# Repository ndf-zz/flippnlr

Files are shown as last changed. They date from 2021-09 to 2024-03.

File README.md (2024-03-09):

# Flippnlr - 4x5 DiY Flipdot Panel

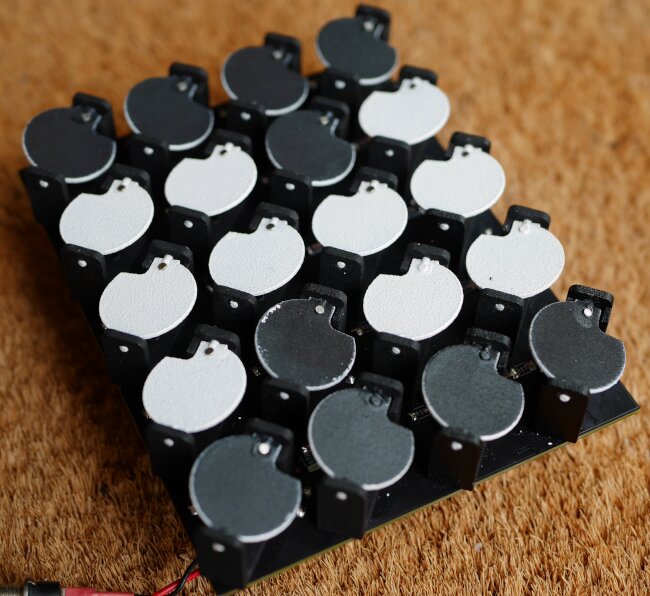
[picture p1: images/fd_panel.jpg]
Panel 4x5 Panel 4x5`


How _not_ to make a DiY electromechanical "Flip-Dot" matrix display.

## Coil Winding

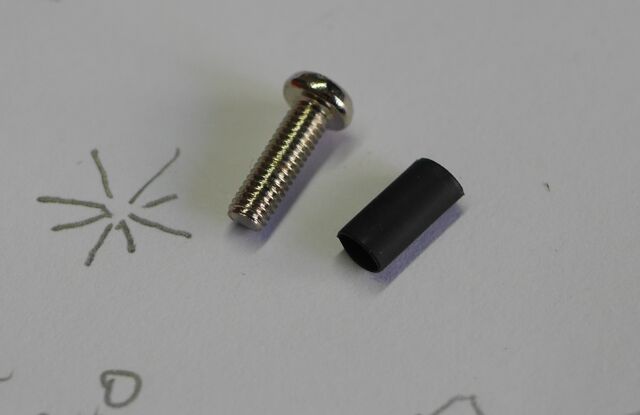
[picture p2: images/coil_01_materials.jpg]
Screw


M3 steel screw and heat shrink tube.

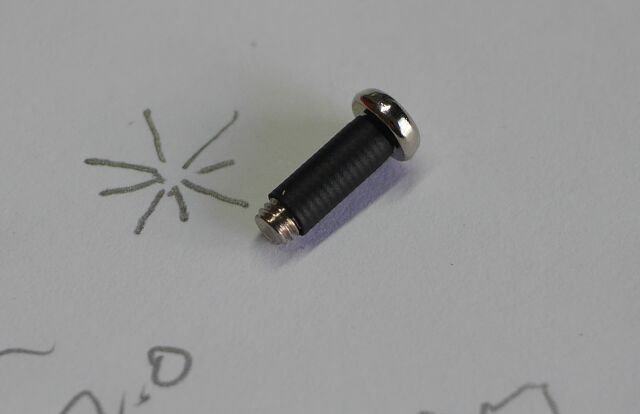
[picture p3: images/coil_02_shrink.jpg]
Shrink


Shrink onto screw.

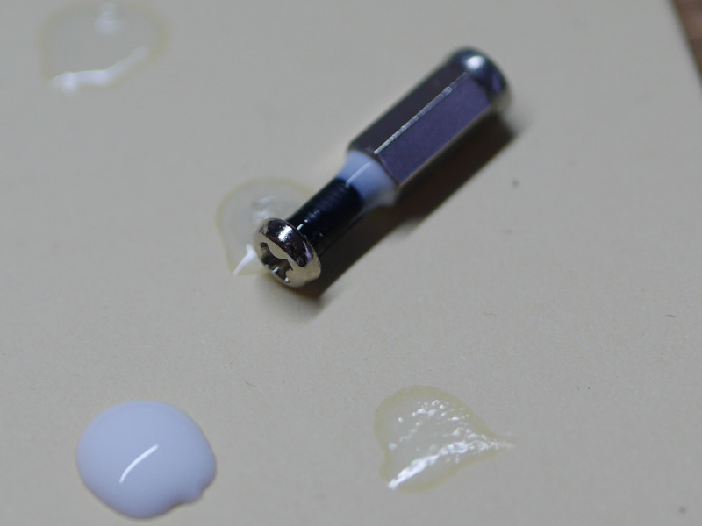
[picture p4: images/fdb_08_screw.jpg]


Add slight glue fillet.

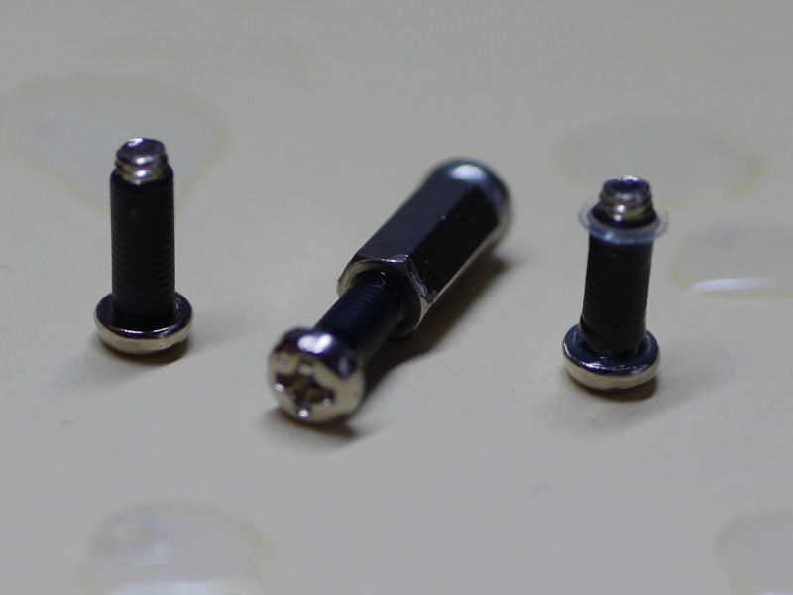
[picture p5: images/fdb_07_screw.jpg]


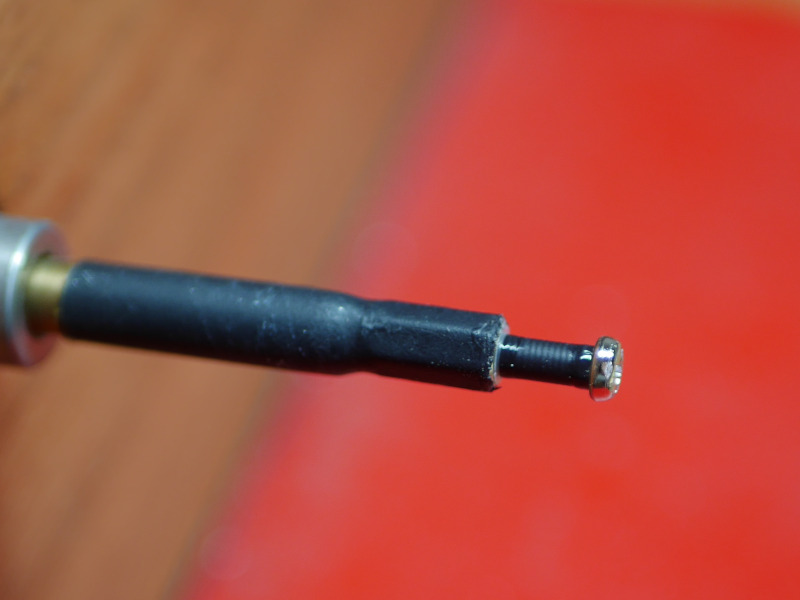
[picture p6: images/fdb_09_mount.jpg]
Mount


Mount in winder.

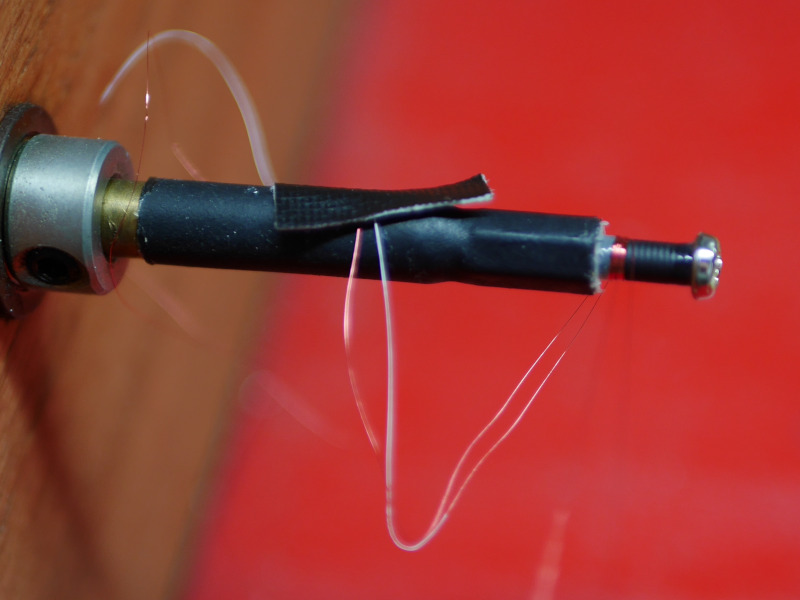
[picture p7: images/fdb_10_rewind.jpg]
Start Wires


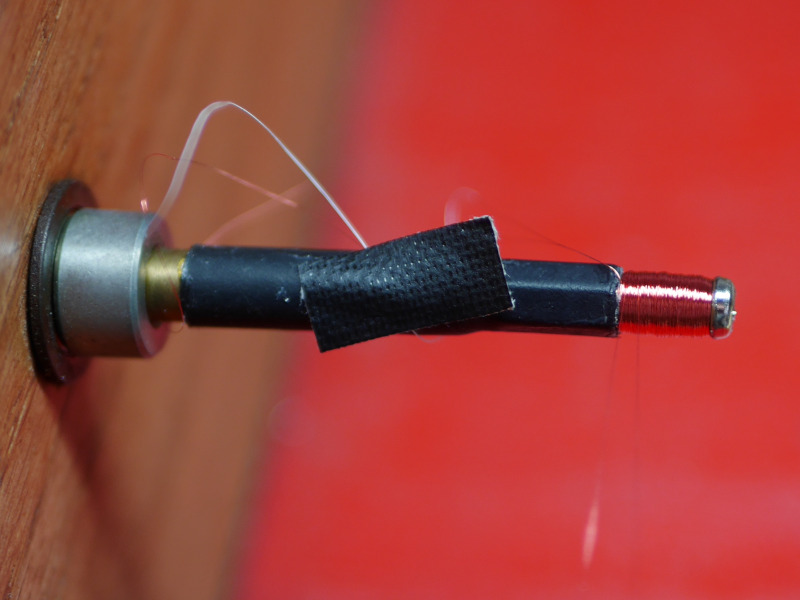
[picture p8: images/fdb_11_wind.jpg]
1000 Turns


Wind about 1000 turns.

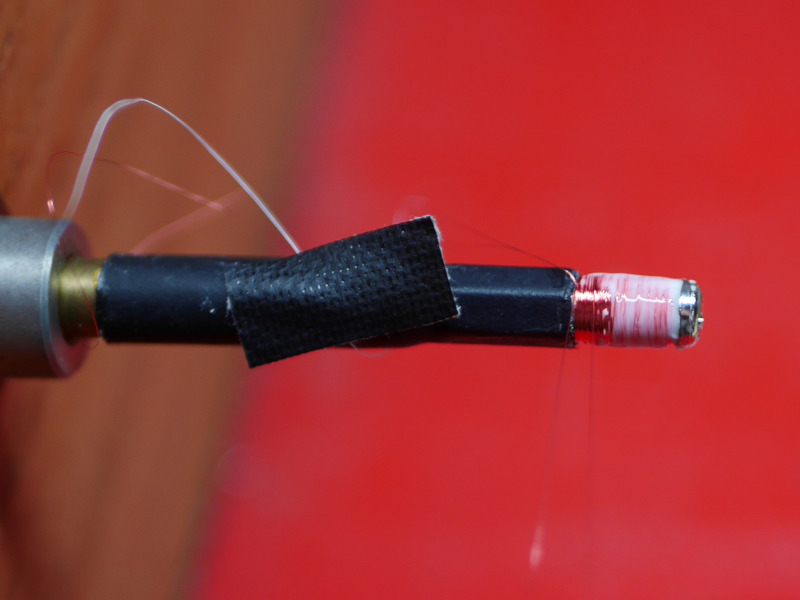
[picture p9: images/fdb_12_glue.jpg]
Glue Coil


Finish with a thin layer of glue.

## Flipdot Mechanism

FreeCAD model: [flipdot.FCStd](flipdot.FCStd)

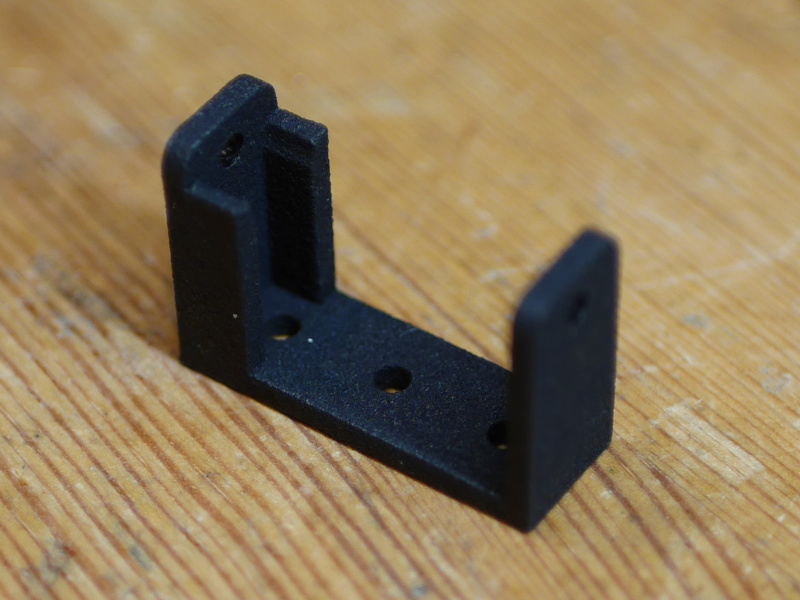
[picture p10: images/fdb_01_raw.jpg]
SLS Body


SLS printed housing.

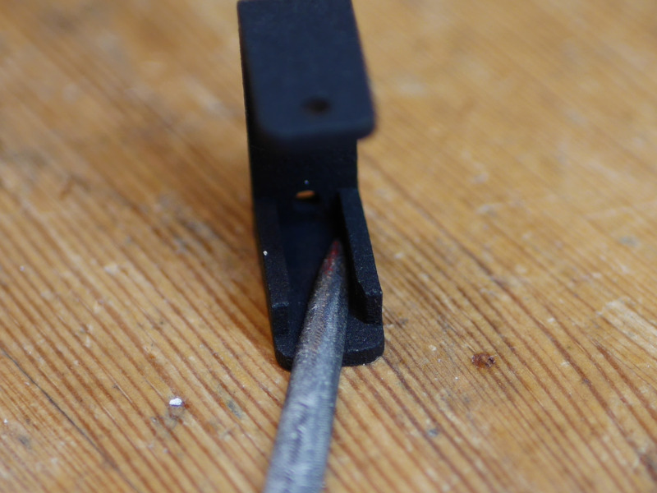
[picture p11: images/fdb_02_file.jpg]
File Housing


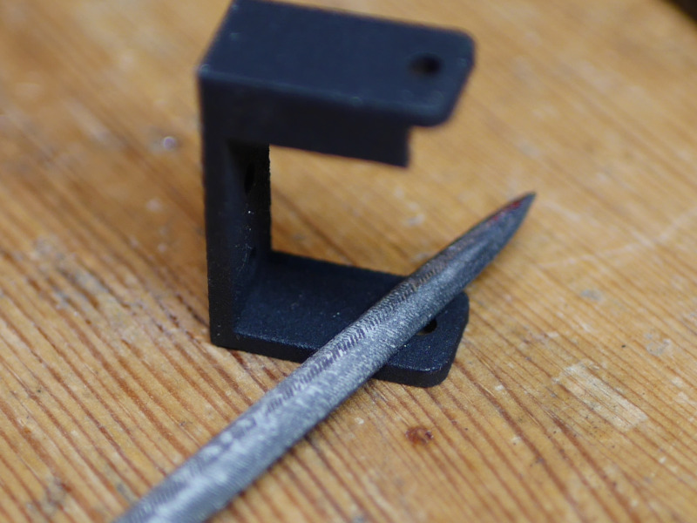
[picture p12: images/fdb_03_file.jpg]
File Mount


File contact areas.

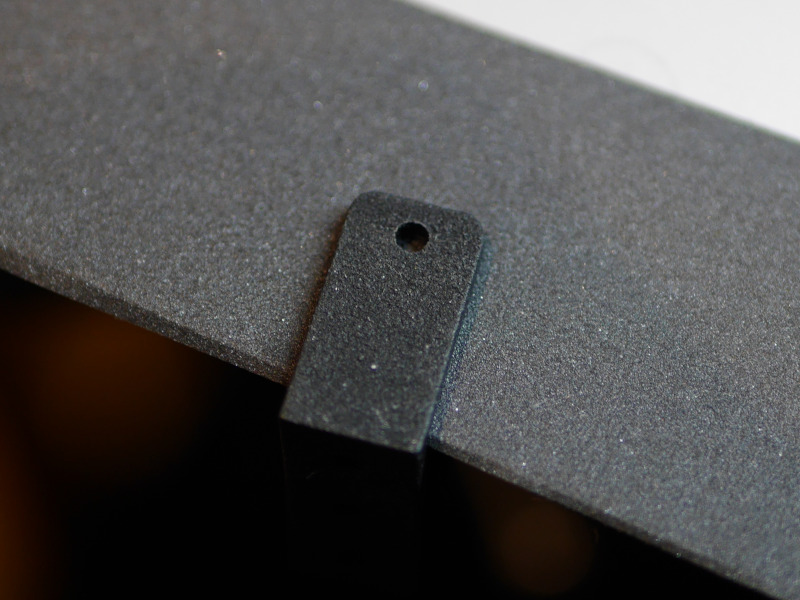
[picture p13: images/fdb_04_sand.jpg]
Smooth Mount


Smooth contact areas with fine sandpaper.

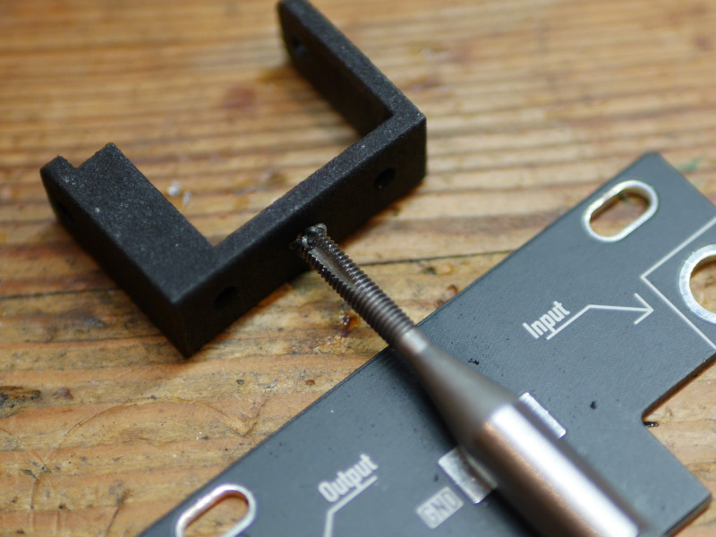
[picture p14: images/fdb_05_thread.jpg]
Tap Mounting Hole


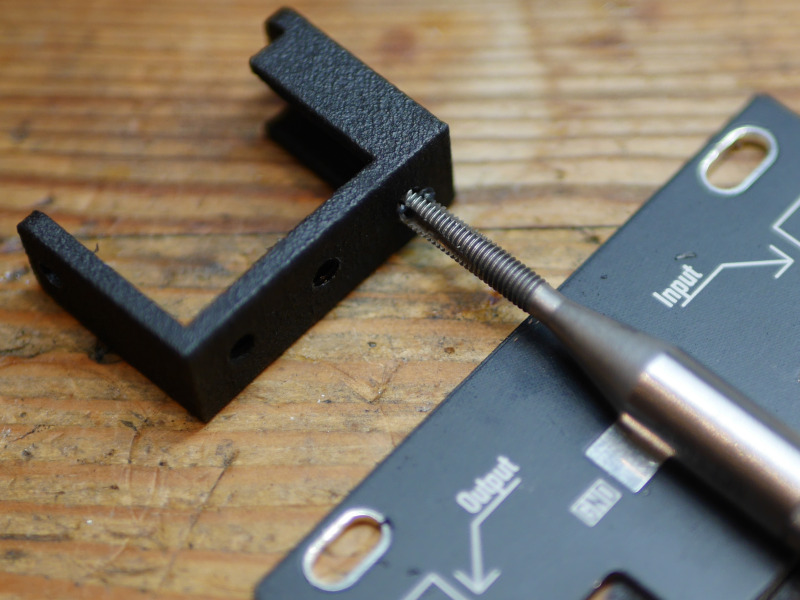
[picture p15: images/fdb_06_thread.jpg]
Tap Coil Hole


Tap mounting and coil holes with M3 thread.

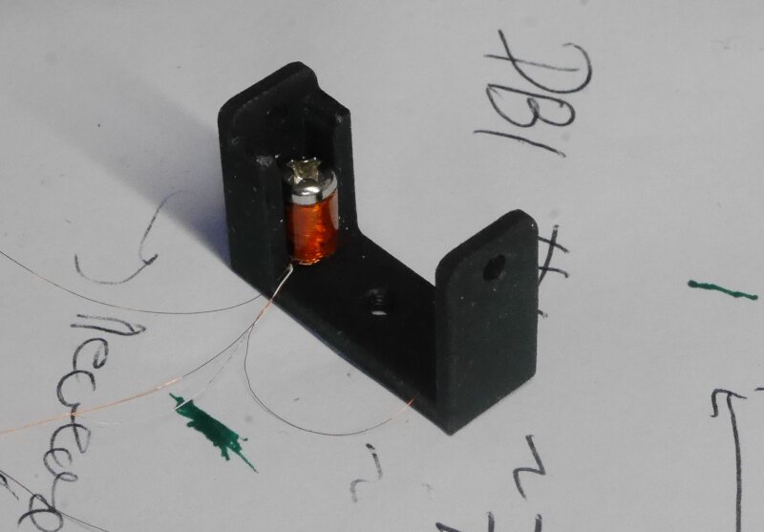
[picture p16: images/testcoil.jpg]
Mount Coil


## Pixel Preparation

## Panel Assembly

Kicad PCB: [flippnlr.pro](flippnlr.pro)

Block Diagram Simplified Schematic

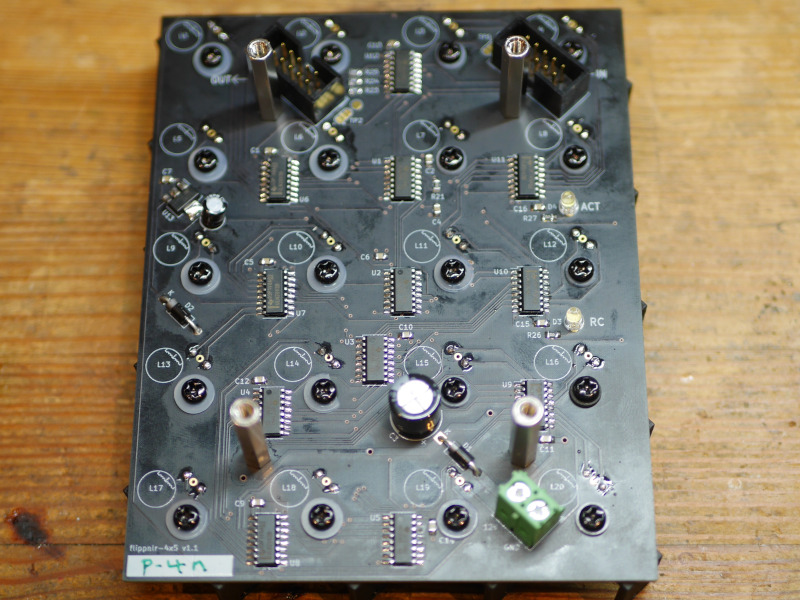
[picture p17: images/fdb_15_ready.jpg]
Solder Components


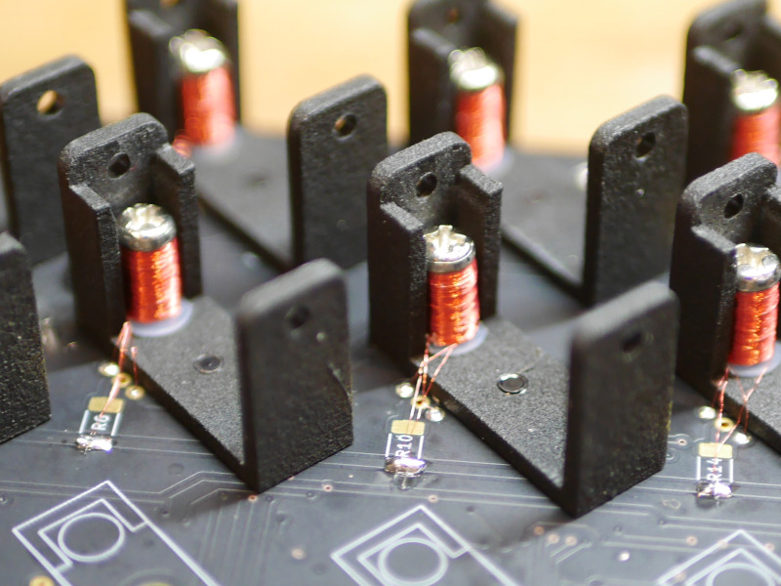
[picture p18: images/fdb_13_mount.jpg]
Attach to Panel


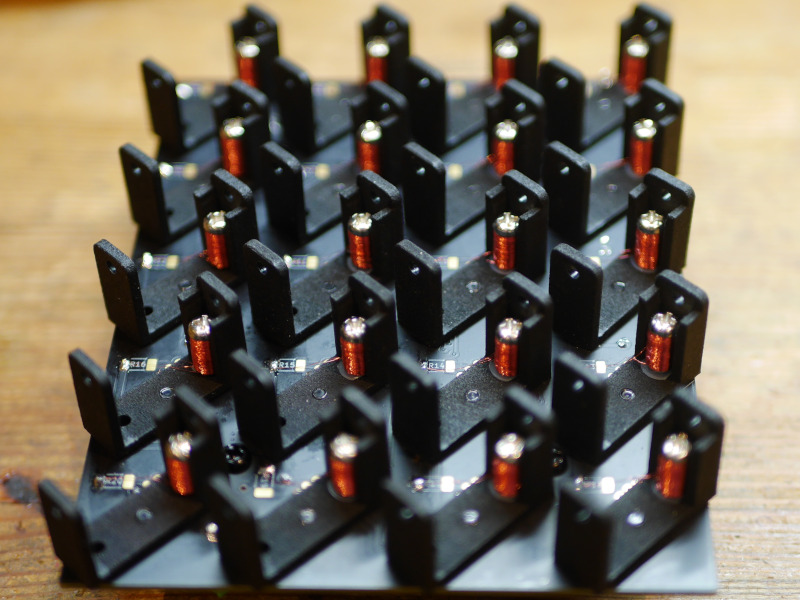
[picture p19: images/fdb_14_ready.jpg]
Ready


## Interface

 - D Data input (SDI)
 - DC Data clock (SCK)
 - RC Latch Clock 

Timing Diagram

## License

CC0 Public Domain

To the extent possible under law, the author(s) have dedicated
all copyright and related and neighboring rights to this software
to the public domain worldwide. This software is distributed
without any warranty.

You should have received a copy of the CC0 Public Domain Dedication
along with this software. If not, see:

http://creativecommons.org/publicdomain/zero/1.0/

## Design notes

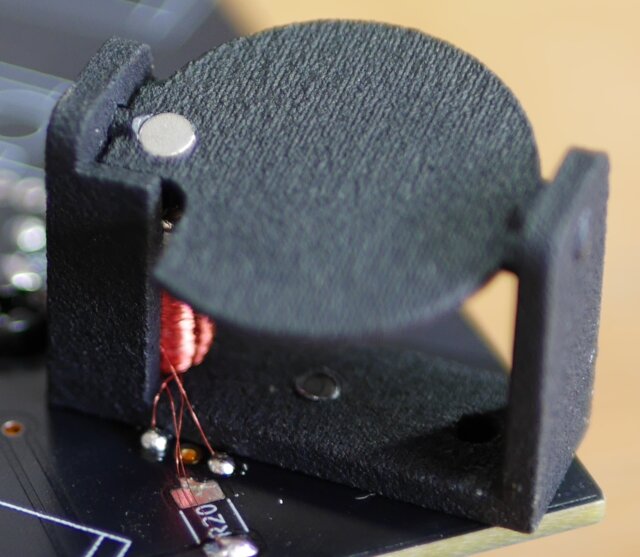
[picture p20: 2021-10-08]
images/fd_single.jpg

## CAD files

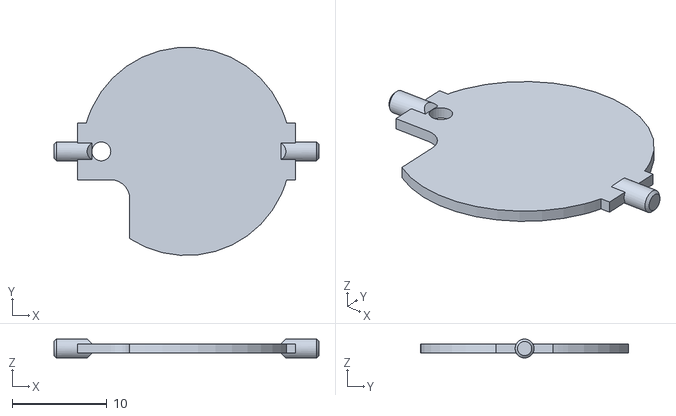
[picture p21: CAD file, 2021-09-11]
flipdot_pixel.stl
28.0 x 21.9 x 2.00

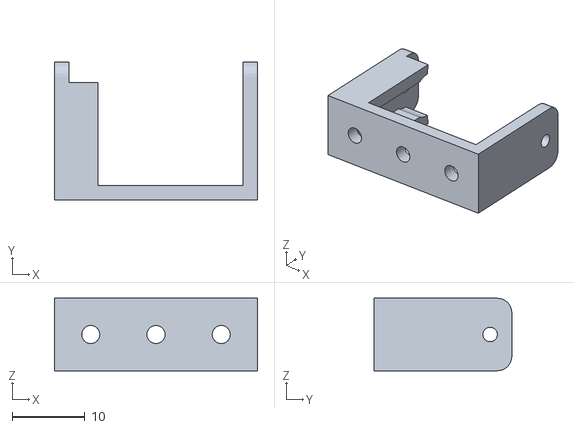
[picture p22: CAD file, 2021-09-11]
flipdot_body.stl
28.0 x 19.0 x 10.0

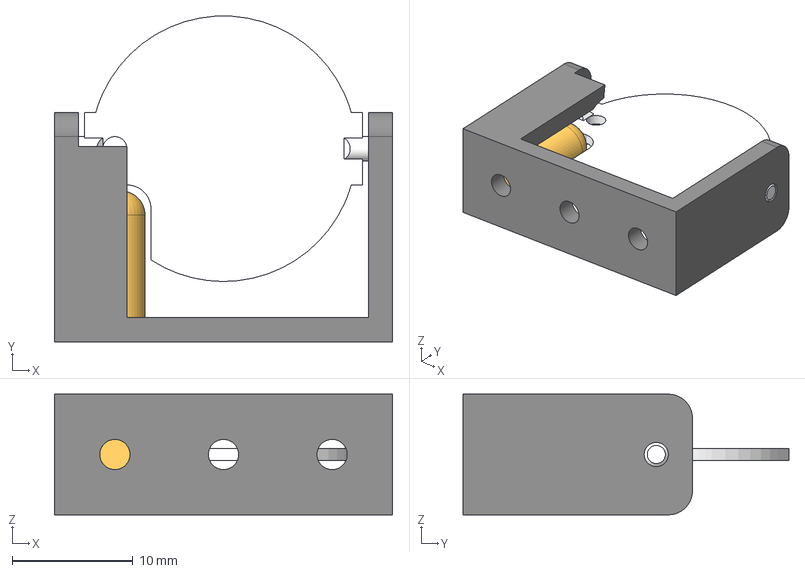
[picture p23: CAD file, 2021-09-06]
flipdot.FCStd
28.0 x 27.0 x 10.0 mm
Pixel
Coil

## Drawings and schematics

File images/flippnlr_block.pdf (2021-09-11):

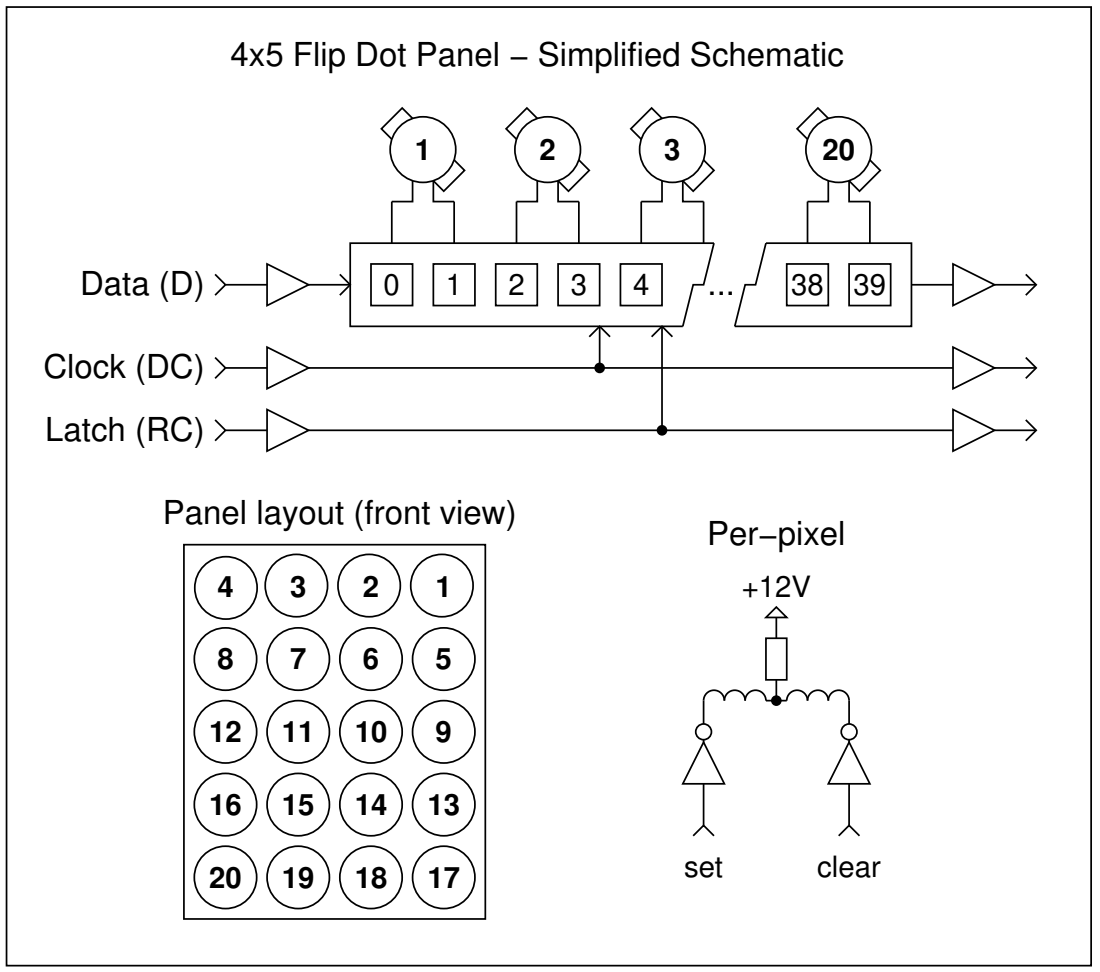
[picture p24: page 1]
Data (D); Latch (RC); Clock (DC); set; clear

4x5 Flip Dot Panel − Simplified Schematic

Per−pixel Panel layout (front view)

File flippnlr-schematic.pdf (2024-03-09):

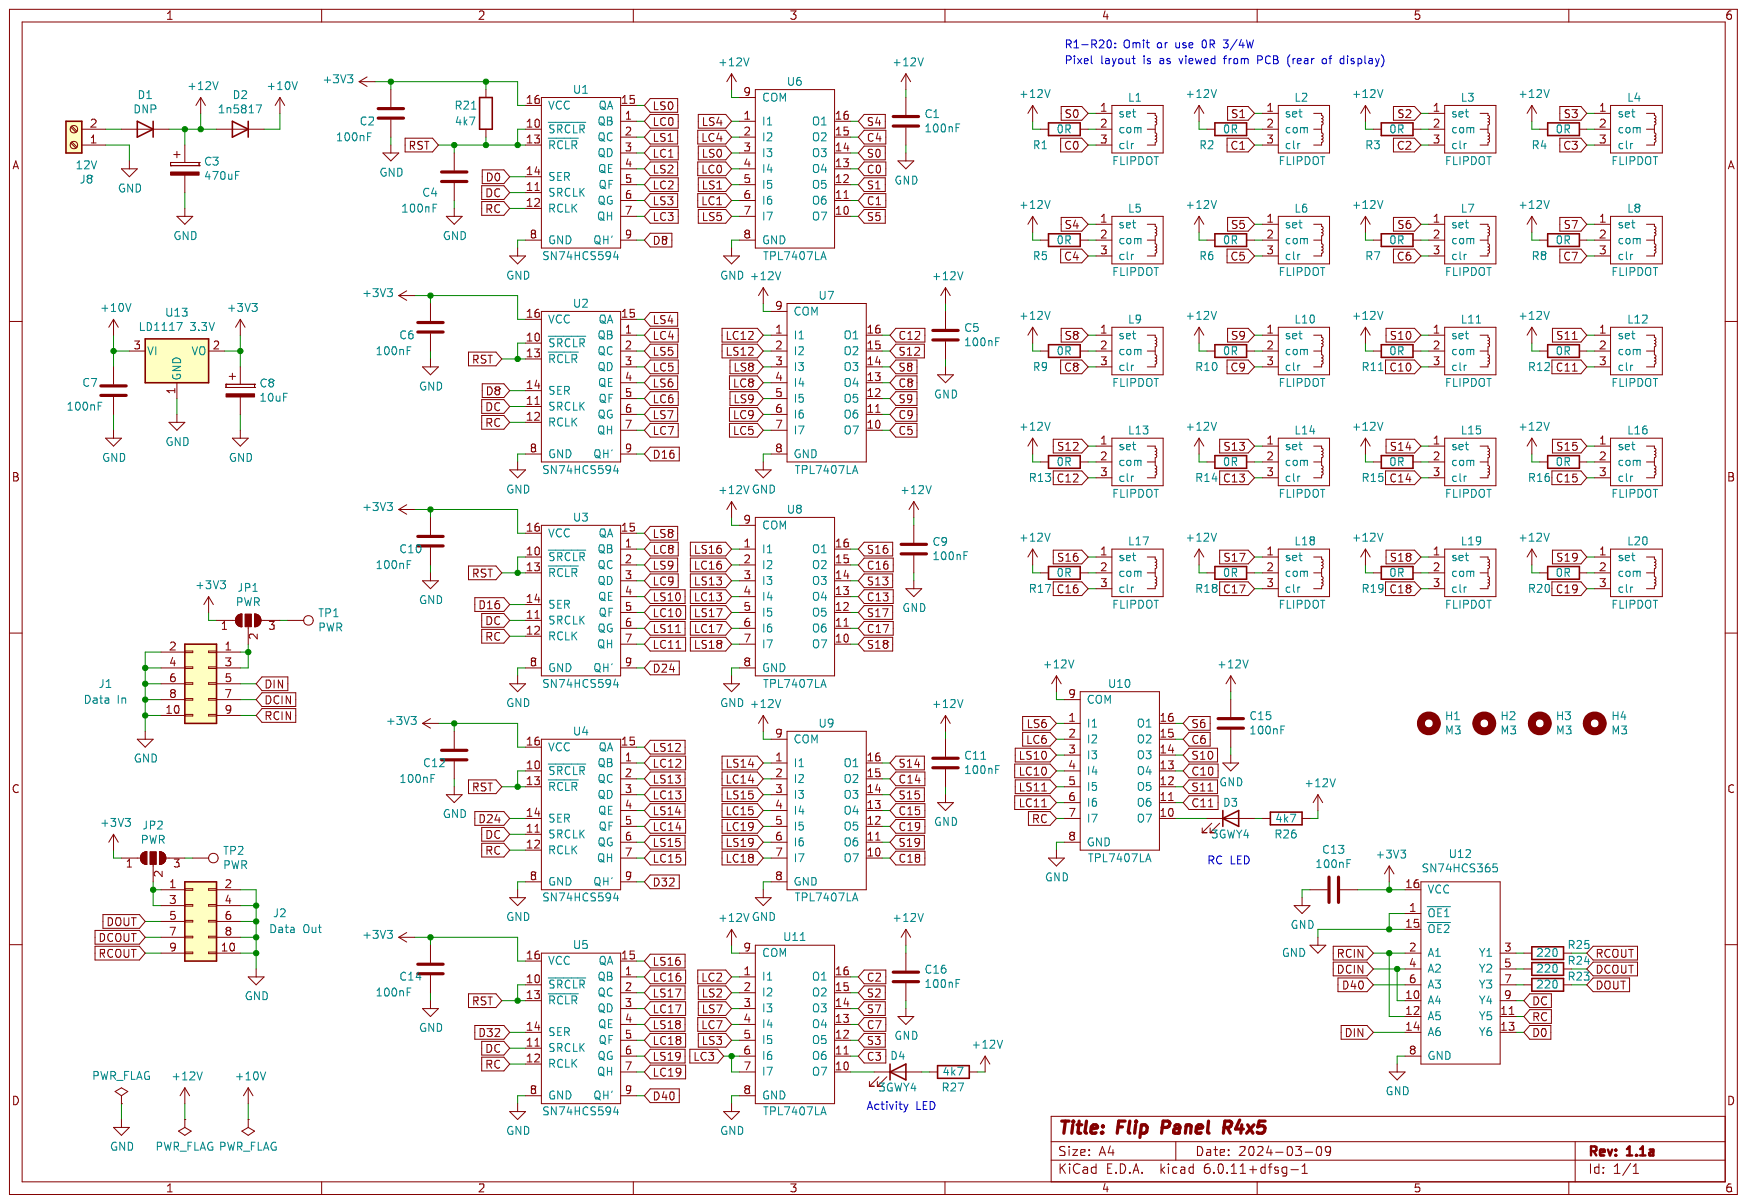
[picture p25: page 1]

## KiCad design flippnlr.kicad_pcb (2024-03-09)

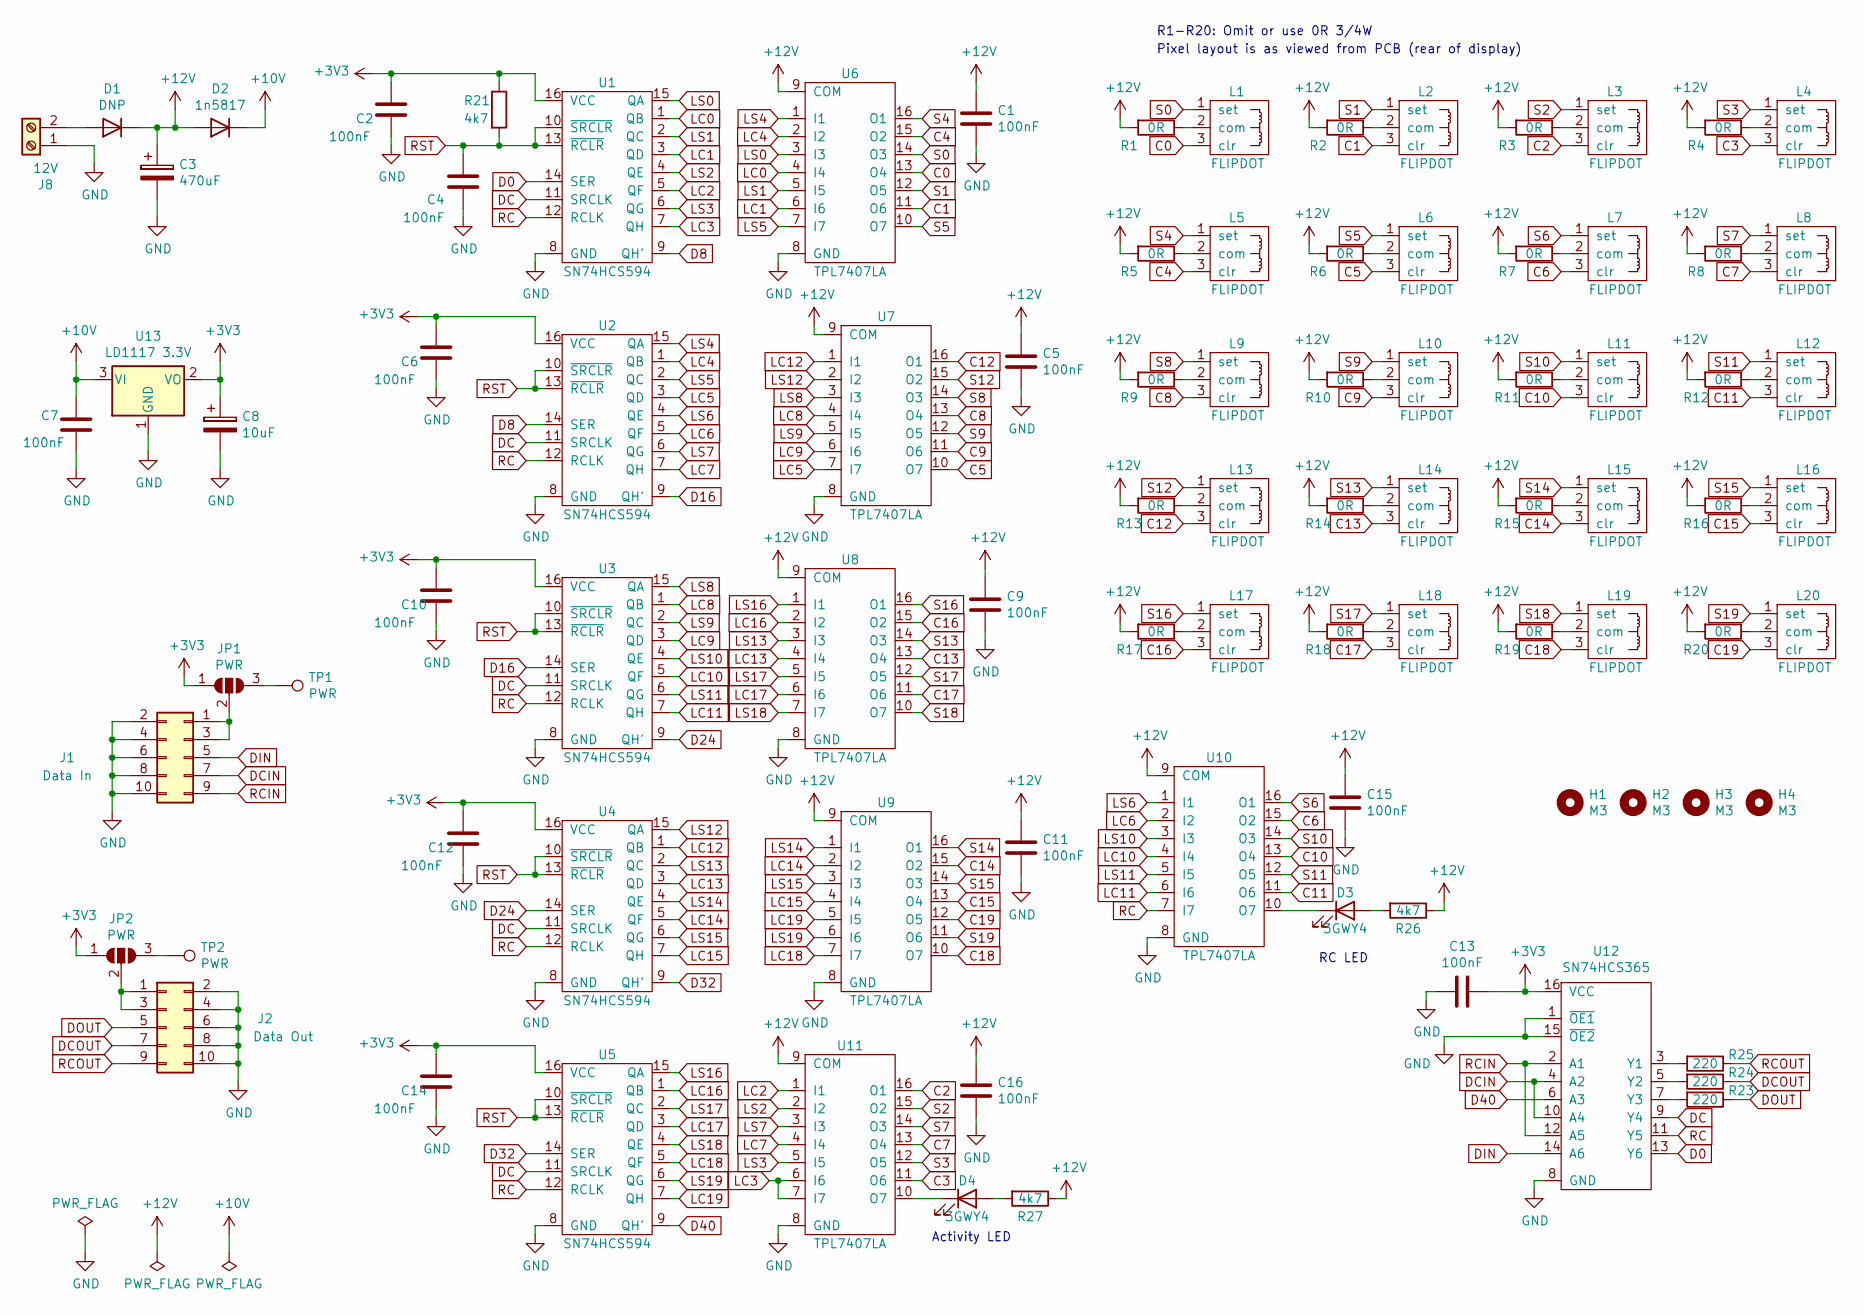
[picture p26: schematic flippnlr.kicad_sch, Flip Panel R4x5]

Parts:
C1, C2, C4, C5, C6, C7, C9, C10, C11, C12, C13, C14, C15, C16: 100nF; C_0805_2012Metric_Pad1.15x1.40mm_HandSolder
C3: 470uF; CP_Radial_D10.0mm_P5.00mm
C8: 10uF; CP_Radial_D5.0mm_P2.50mm
D1: DNP; D_A-405_P10.16mm_Horizontal
D2: 1n5817; D_A-405_P10.16mm_Horizontal
D3, D4: 3GWY4; LED_D3.0mm
H1, H2, H3, H4: M3; MountingHole_3.2mm_M3
J1: Data In; IDC-Header_2x05_P2.54mm_Vertical
J2: Data Out; IDC-Header_2x05_P2.54mm_Vertical
J8: 12V; TerminalBlock_Phoenix_PT-1,5-2-5.0-H_1x02_P5.00mm_Horizontal
JP1, JP2: PWR; SolderJumper-3_P1.3mm_Open_RoundedPad1.0x1.5mm
L1, L2, L3, L4, L5, L6, L7, L8, L9, L10, L11, L12, L13, L14, L15, L16, L17, L18, L19, L20: FLIPDOT; Flipdot
R1, R2, R3, R4, R5, R6, R7, R8, R9, R10, R11, R12, R13, R14, R15, R16, R17, R18, R19, R20: 0R; R_2010_5025Metric_Pad1.52x2.65mm_HandSolder
R21, R26, R27: 4k7; R_0805_2012Metric_Pad1.15x1.40mm_HandSolder
R23, R24, R25: 220; R_0805_2012Metric_Pad1.15x1.40mm_HandSolder
TP1, TP2: PWR; TestPoint_Pad_D2.0mm
U1, U2, U3, U4, U5: SN74HCS594; SOP-16_4.4x10.4mm_P1.27mm
U6, U7, U8, U9, U10, U11: TPL7407LA; SOP-16_4.4x10.4mm_P1.27mm
U12: SN74HCS365; SOP-16_4.4x10.4mm_P1.27mm
U13: LD1117 3.3V; SOT-223-3_TabPin2

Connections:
+3V3: C2.1, C6.1, C8.1, C10.1, C12.1, C13.1, C14.1, JP1.1 (A), JP2.1 (A), R21.1, U1.16 (VCC), U2.16 (VCC), U3.16 (VCC), U4.16 (VCC), U5.16 (VCC), U12.16 (VCC), U13.2 (VO)
+10V: C7.1, D2.1 (K), U13.3 (VI)
+12V: C1.1, C3.1, C5.1, C9.1, C11.1, C15.1, C16.1, D1.1 (K), D2.2 (A), R1.2, R2.2, R3.2, R4.2, R5.2, R6.2, R7.2, R8.2, R9.2, R10.2, R11.2, R12.2, R13.2, R14.2, R15.2, R16.2, R17.2, R18.2, R19.2, R20.2, R26.1, R27.1, U6.9 (COM), U7.9 (COM), U8.9 (COM), U9.9 (COM), U10.9 (COM), U11.9 (COM)
C0: L1.3 (clr), U6.13 (O4)
C1: L2.3 (clr), U6.11 (O6)
C2: L3.3 (clr), U11.16 (O1)
C3: L4.3 (clr), U11.11 (O6)
C4: L5.3 (clr), U6.15 (O2)
C5: L6.3 (clr), U7.10 (O7)
C6: L7.3 (clr), U10.15 (O2)
C7: L8.3 (clr), U11.13 (O4)
C8: L9.3 (clr), U7.13 (O4)
C9: L10.3 (clr), U7.11 (O6)
C10: L11.3 (clr), U10.13 (O4)
C11: L12.3 (clr), U10.11 (O6)
C12: L13.3 (clr), U7.16 (O1)
C13: L14.3 (clr), U8.13 (O4)
C14: L15.3 (clr), U9.15 (O2)
C15: L16.3 (clr), U9.13 (O4)
C16: L17.3 (clr), U8.15 (O2)
C17: L18.3 (clr), U8.11 (O6)
C18: L19.3 (clr), U9.10 (O7)
C19: L20.3 (clr), U9.12 (O5)
D0: U1.14 (SER), U12.13 (Y6)
D8: U1.9 (QH'), U2.14 (SER)
D16: U2.9 (QH'), U3.14 (SER)
D24: U3.9 (QH'), U4.14 (SER)
D32: U4.9 (QH'), U5.14 (SER)
D40: U5.9 (QH'), U12.6 (A3)
DC: U1.11 (SRCLK), U2.11 (SRCLK), U3.11 (SRCLK), U4.11 (SRCLK), U5.11 (SRCLK), U12.9 (Y4)
DCIN: J1.7, U12.4 (A2), U12.10 (A4)
DCOUT: J2.7, R24.1
DIN: J1.5, U12.14 (A6)
DOUT: J2.5, R23.1
GND: C1.2, C2.2, C3.2, C4.1, C5.2, C6.2, C7.2, C8.2, C9.2, C10.2, C11.2, C12.2, C13.2, C14.2, C15.2, C16.2, J1.2, J1.4, J1.6, J1.8, J1.10, J2.2, J2.4, J2.6, J2.8, J2.10, J8.1, U1.8 (GND), U2.8 (GND), U3.8 (GND), U4.8 (GND), U5.8 (GND), U6.8 (GND), U7.8 (GND), U8.8 (GND), U9.8 (GND), U10.8 (GND), U11.8 (GND), U12.1 (~OE1), U12.8 (GND), U12.15 (~OE2), U13.1 (GND)
LC0: U1.1 (QB), U6.4 (I4)
LC1: U1.3 (QD), U6.6 (I6)
LC2: U1.5 (QF), U11.1 (I1)
LC3: U1.7 (QH), U11.6 (I6), U11.7 (I7)
LC4: U2.1 (QB), U6.2 (I2)
LC5: U2.3 (QD), U7.7 (I7)
LC6: U2.5 (QF), U10.2 (I2)
LC7: U2.7 (QH), U11.4 (I4)
LC8: U3.1 (QB), U7.4 (I4)
LC9: U3.3 (QD), U7.6 (I6)
LC10: U3.5 (QF), U10.4 (I4)
LC11: U3.7 (QH), U10.6 (I6)
LC12: U4.1 (QB), U7.1 (I1)
LC13: U4.3 (QD), U8.4 (I4)
LC14: U4.5 (QF), U9.2 (I2)
LC15: U4.7 (QH), U9.4 (I4)
LC16: U5.1 (QB), U8.2 (I2)
LC17: U5.3 (QD), U8.6 (I6)
LC18: U5.5 (QF), U9.7 (I7)
LC19: U5.7 (QH), U9.5 (I5)
LS0: U1.15 (QA), U6.3 (I3)
LS1: U1.2 (QC), U6.5 (I5)
LS2: U1.4 (QE), U11.2 (I2)
LS3: U1.6 (QG), U11.5 (I5)
LS4: U2.15 (QA), U6.1 (I1)
LS5: U2.2 (QC), U6.7 (I7)
LS6: U2.4 (QE), U10.1 (I1)
LS7: U2.6 (QG), U11.3 (I3)
LS8: U3.15 (QA), U7.3 (I3)
LS9: U3.2 (QC), U7.5 (I5)
LS10: U3.4 (QE), U10.3 (I3)
LS11: U3.6 (QG), U10.5 (I5)
LS12: U4.15 (QA), U7.2 (I2)
LS13: U4.2 (QC), U8.3 (I3)
LS14: U4.4 (QE), U9.1 (I1)
LS15: U4.6 (QG), U9.3 (I3)
LS16: U5.15 (QA), U8.1 (I1)
LS17: U5.2 (QC), U8.5 (I5)
LS18: U5.4 (QE), U8.7 (I7)
LS19: U5.6 (QG), U9.6 (I6)
unnamed: D1.2 (A), J8.2
unnamed: D3.1 (K), U10.10 (O7)
unnamed: D3.2 (A), R26.2
unnamed: D4.1 (K), U11.10 (O7)
unnamed: D4.2 (A), R27.2
unnamed: J1.1, J1.3, JP1.2 (C)
unnamed: J2.1, J2.3, JP2.2 (C)
unnamed: JP1.3 (B), TP1.1
unnamed: JP2.3 (B), TP2.1
unnamed: L1.2 (com), R1.1
unnamed: L2.2 (com), R2.1
unnamed: L3.2 (com), R3.1
unnamed: L4.2 (com), R4.1
unnamed: L5.2 (com), R5.1
unnamed: L6.2 (com), R6.1
unnamed: L7.2 (com), R7.1
unnamed: L8.2 (com), R8.1
unnamed: L9.2 (com), R9.1
unnamed: L10.2 (com), R10.1
unnamed: L11.2 (com), R11.1
unnamed: L12.2 (com), R12.1
unnamed: L13.2 (com), R13.1
unnamed: L14.2 (com), R14.1
unnamed: L15.2 (com), R15.1
unnamed: L16.2 (com), R16.1
unnamed: L17.2 (com), R17.1
unnamed: L18.2 (com), R18.1
unnamed: L19.2 (com), R19.1
unnamed: L20.2 (com), R20.1
unnamed: R23.2, U12.7 (Y3)
unnamed: R24.2, U12.5 (Y2)
unnamed: R25.2, U12.3 (Y1)
RC: U1.12 (RCLK), U2.12 (RCLK), U3.12 (RCLK), U4.12 (RCLK), U5.12 (RCLK), U10.7 (I7), U12.11 (Y5)
RCIN: J1.9, U12.2 (A1), U12.12 (A5)
RCOUT: J2.9, R25.1
RST: C4.2, R21.2, U1.10 (~SRCLR), U1.13 (~RCLR), U2.10 (~SRCLR), U2.13 (~RCLR), U3.10 (~SRCLR), U3.13 (~RCLR), U4.10 (~SRCLR), U4.13 (~RCLR), U5.10 (~SRCLR), U5.13 (~RCLR)
S0: L1.1 (set), U6.14 (O3)
S1: L2.1 (set), U6.12 (O5)
S2: L3.1 (set), U11.15 (O2)
S3: L4.1 (set), U11.12 (O5)
S4: L5.1 (set), U6.16 (O1)
S5: L6.1 (set), U6.10 (O7)
S6: L7.1 (set), U10.16 (O1)
S7: L8.1 (set), U11.14 (O3)
S8: L9.1 (set), U7.14 (O3)
S9: L10.1 (set), U7.12 (O5)
S10: L11.1 (set), U10.14 (O3)
S11: L12.1 (set), U10.12 (O5)
S12: L13.1 (set), U7.15 (O2)
S13: L14.1 (set), U8.14 (O3)
S14: L15.1 (set), U9.16 (O1)
S15: L16.1 (set), U9.14 (O3)
S16: L17.1 (set), U8.16 (O1)
S17: L18.1 (set), U8.12 (O5)
S18: L19.1 (set), U8.10 (O7)
S19: L20.1 (set), U9.11 (O6)

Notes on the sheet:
R1-R20: Omit or use 0R 3/4W
RC LED
Pixel layout is as viewed from PCB (rear of display)
Activity LED

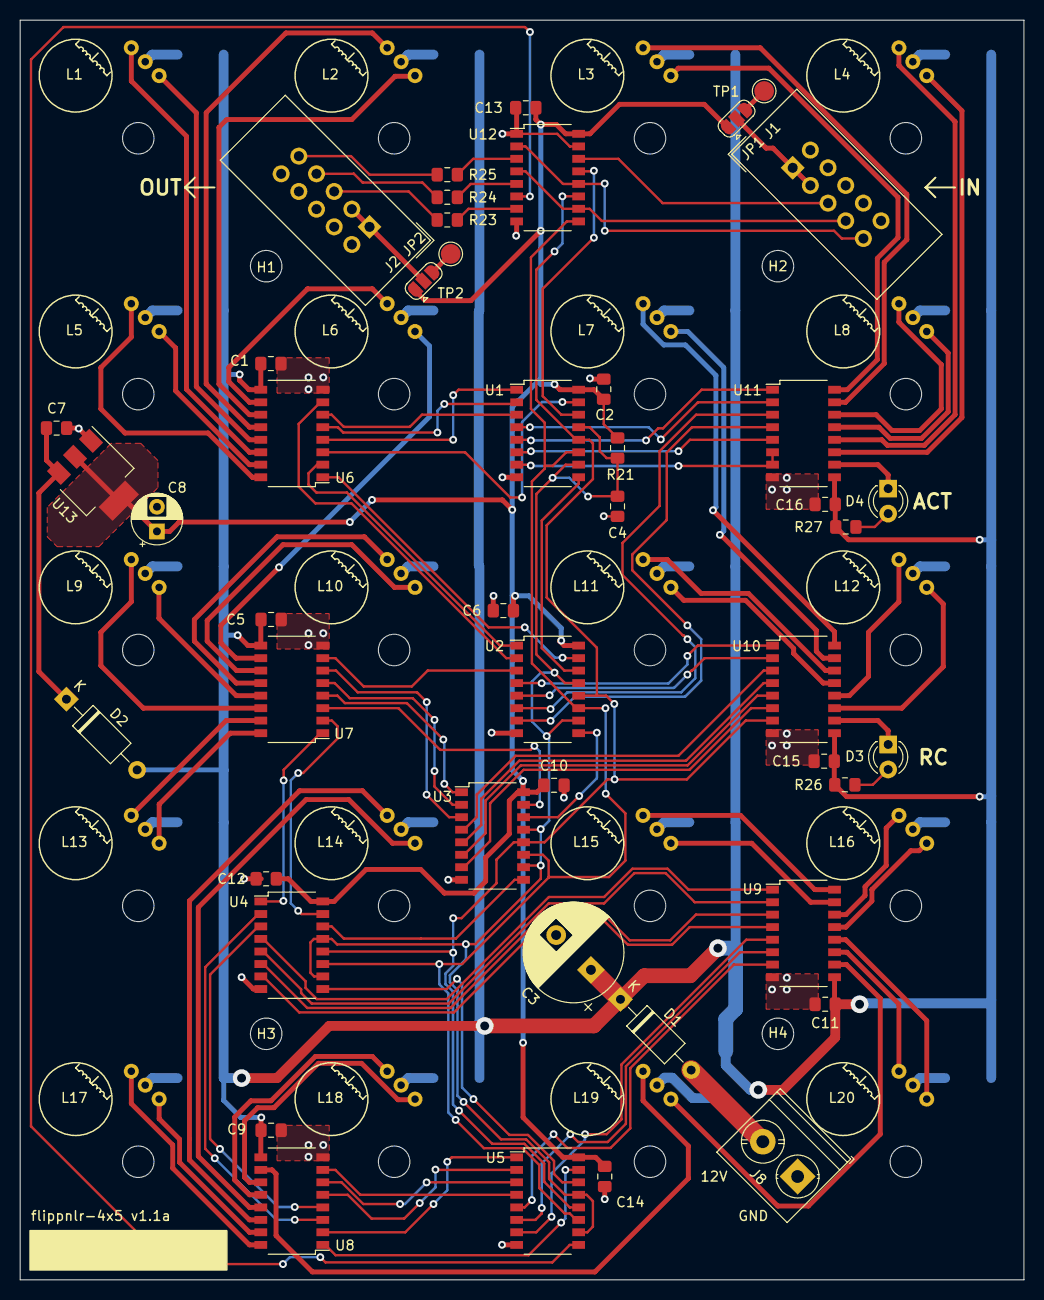
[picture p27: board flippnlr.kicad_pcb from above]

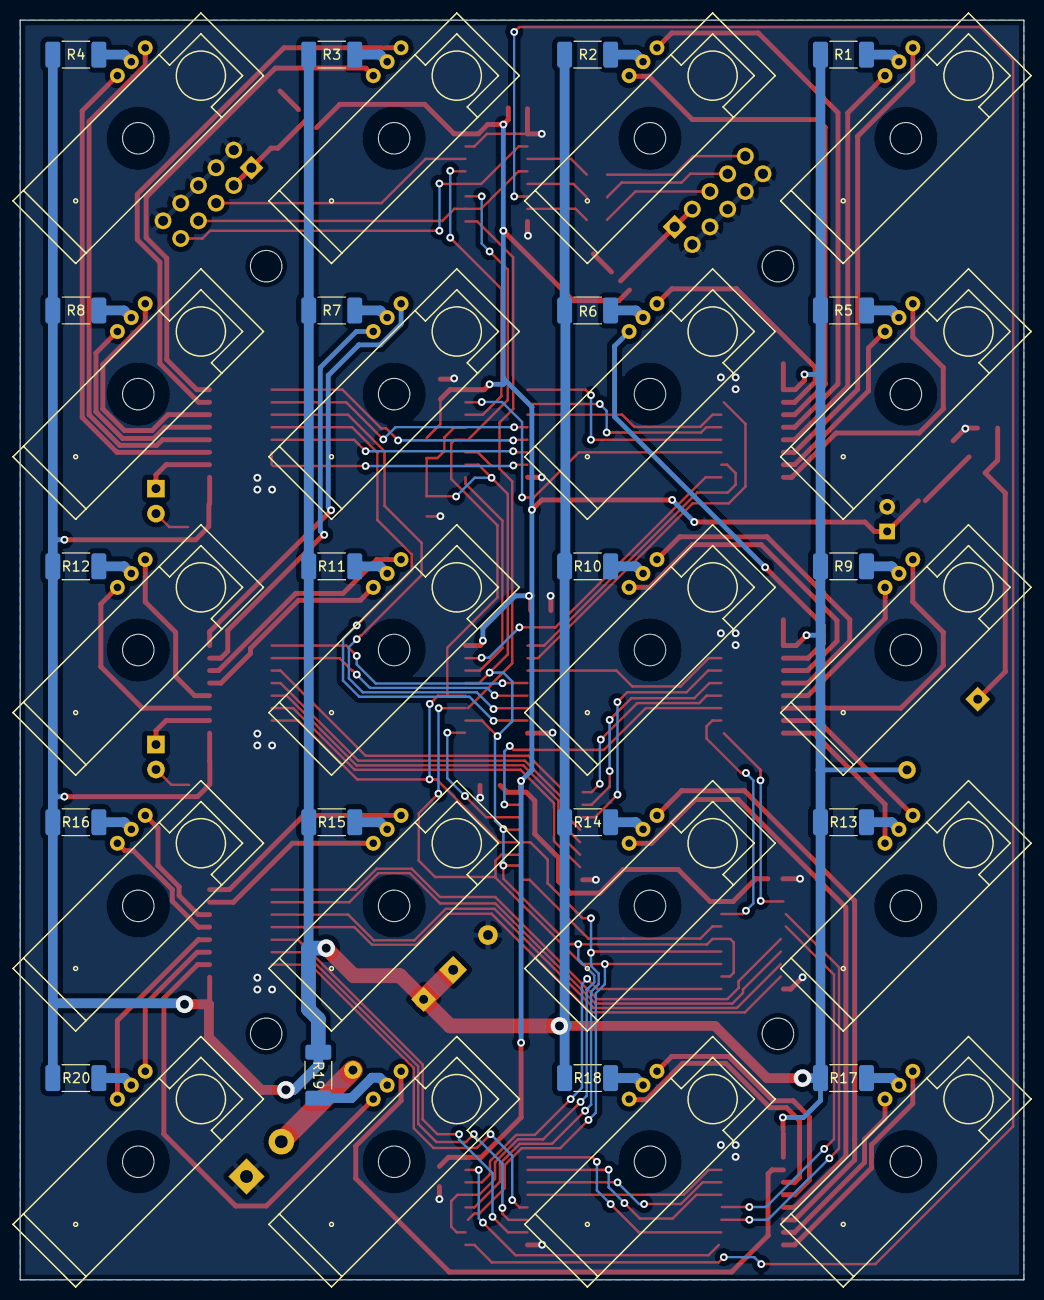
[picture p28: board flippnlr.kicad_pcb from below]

Board: 2 copper layers, 102.0 x 128.0 mm, 90 parts (20 on the bottom side), 131 nets.

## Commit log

2021-09-06 add pixel cad model
    [flipdot.FCStd]
2021-09-06 add kicad project
    [flippnlr.kicad_pcb, flippnlr.sch]
2021-09-11 fix kicad lib path and begin layout
    [flipdot_body.stl, flipdot_pixel.stl, flippnlr.kicad_pcb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]
2021-09-12 reroute signals slightly
    [flippnlr.kicad_pcb, flippnlr.sch]
2021-09-12 pcb roughly routed
    [flippnlr.kicad_pcb]
2021-09-14 correct mis-wired U5
    [flippnlr.kicad_pcb, flippnlr.sch]
2021-09-14 correct Lx3/Lx7
    [flippnlr.kicad_pcb, flippnlr.sch]
2021-09-15 prepare for gerbers
    [flippnlr.kicad_pcb]
2021-09-15 first prototype
    [flippnlr.kicad_pcb, flippnlr.sch]
2021-10-09 alter start wire to avoid shorts
2021-10-20 add panel image and spi timing
2024-03-09 Update to Kicad v6
    [flippnlr.kicad_pcb, flippnlr.kicad_sch, flippnlr.sch]
2024-03-09 Rename repository to match Kicad project
